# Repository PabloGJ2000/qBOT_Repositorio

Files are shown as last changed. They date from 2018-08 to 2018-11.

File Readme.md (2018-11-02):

# qBOT_Repositorio

## Información
* Autor: Pablo García Jaén (twitter: [@pablogarciajaen](https://twitter.com/PabloGarciaJaen)  )
* Web: http://qbotproject.com/
* Licencia: Creative Common CC BY-NC-SA 
* qBOT está basado en el mismo concepto de los Nanobots de la película Big Hero 6.

## Materiales
| Artículo | Cantidad* |
| --- | --- |
| Arduino Nano | 1 |
| GearMotor N20 | 3 |
| Acoplamiento para el eje N20 (3mm) | 3 |
| GearMotor N20 Eje m4 | 3 |
| Servo Analog SUMO1109 | 3 |
| Aspas Servo | 3 |
| Imán Neodimio N42 9x3mm | 6 |
| Pin Macho (4 pines juntos) | 3 |
| Pin Hembra (4 pines juntos) | 12 |
| Driver de motores SN754410 | 3 |
| Extensor de pines MCP23008 | 1 |
| Potenciometro 10k | 3 |
| Tornillería | - |
| 3D | - |

* *CANTIDAD PARA UN qBOT

## Hazlo tu mismo (DIY)

`Parte 1: Cara A` 

#### 	Diseño:

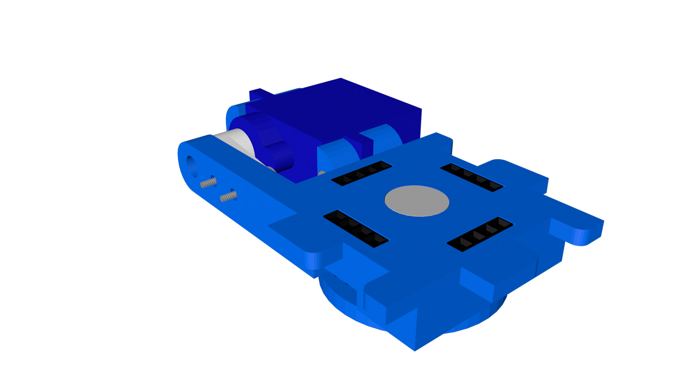
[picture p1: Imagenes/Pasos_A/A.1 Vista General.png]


#### 	Archivos 3D:

Haz click para descargarlas

- [CaraA.1_Pieza1.stl](https://github.com/PabloGarciaJaen/qBOT_Repositorio/blob/master/Archivos%203D/CaraA.1_Pieza1.stl)

- [CaraA.1_Pieza2.stl](https://github.com/PabloGarciaJaen/qBOT_Repositorio/blob/master/Archivos%203D/CaraA.1_Pieza2.stl)

- [CaraA.1_Pieza3.stl](https://github.com/PabloGarciaJaen/qBOT_Repositorio/blob/master/Archivos%203D/CaraA.1_Pieza3.stl)

//Nota_1: Los archivos están optimizados para una correcta impresión 3D sin soportes

//Nota_2: Es posible que algunas tengas que quitar el hueco para los tornillos o limar algunas partes.

#### 	Componentes:

| Componente | Cantdidad |
| --- | --- |
| Servo Analog SUMO1109 | 1 |
| Aspa servo | 1 |
| Imán Neodimio N42 9x3mm | 1 |
| Pin Hembra (4 pines juntos) | 3 |
| Tornillo eje servo | 1 |
| Tornillo anclaje | 2 |
| Tornillo soporte | 2 |

#### Montaje:

1. Pega las piezas *CaraA.1_Pieza1.stl* y *CaraA.1_Pieza2.stl*.

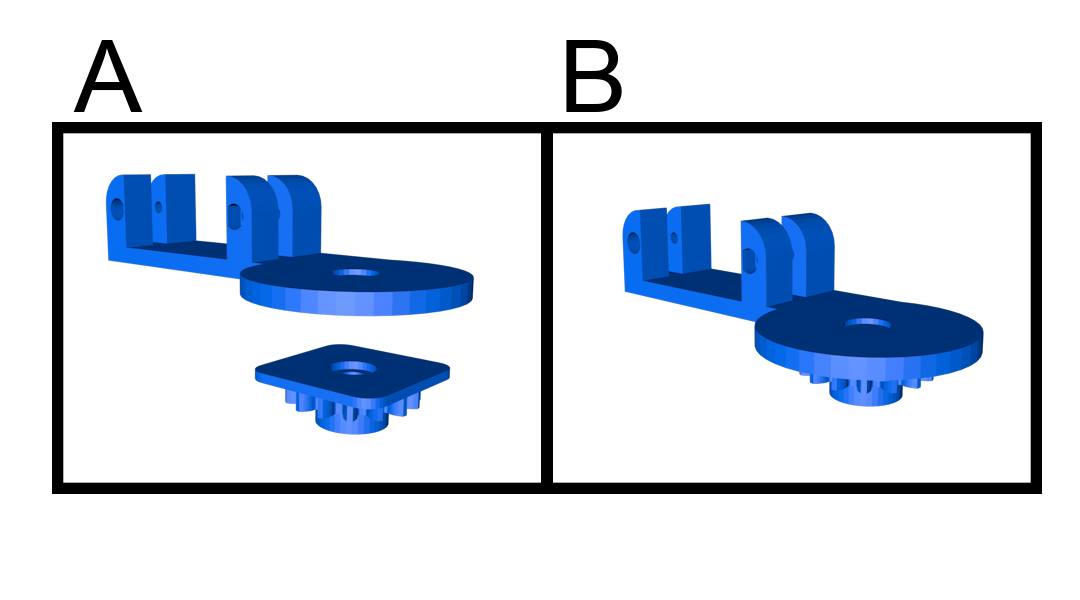
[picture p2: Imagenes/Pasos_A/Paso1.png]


2. Introduce el tornillo del eje por el aspa del servo.

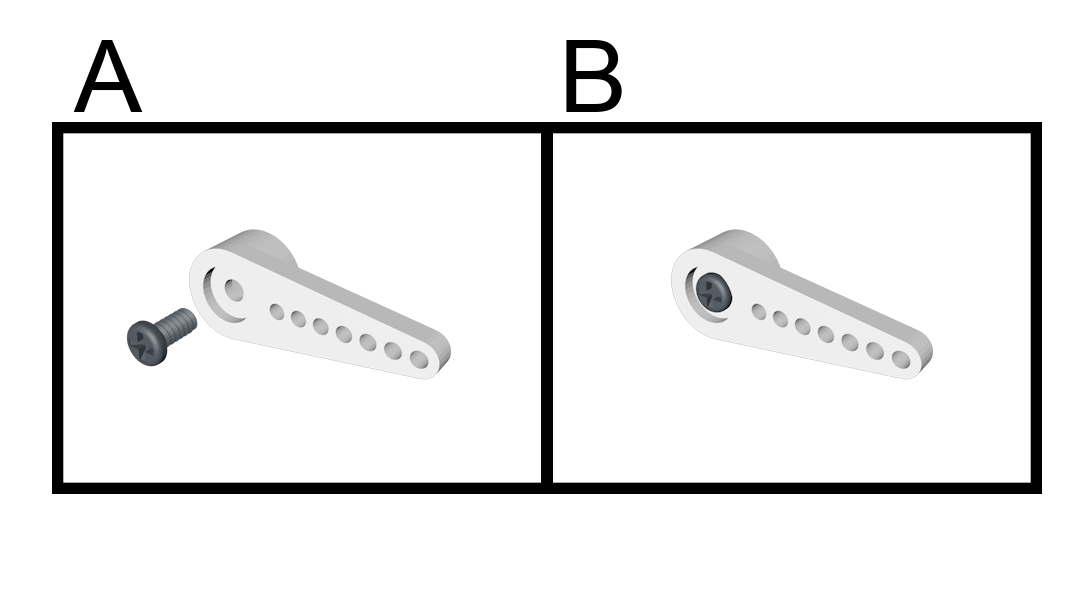
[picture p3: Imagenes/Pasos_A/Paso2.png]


3. Atornilla la pieza blanca del servo a *CaraA.1_Pieza3.stl*.

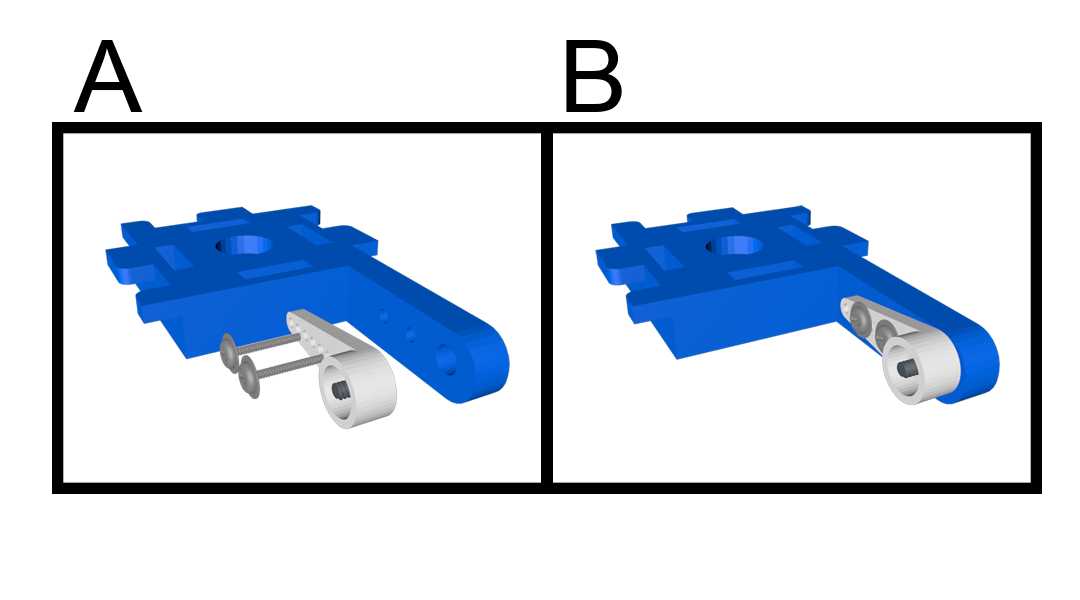
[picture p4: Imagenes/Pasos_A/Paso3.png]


4. Introduce el iman de neodimio y los pines hembra en sus correspondientes orificios.

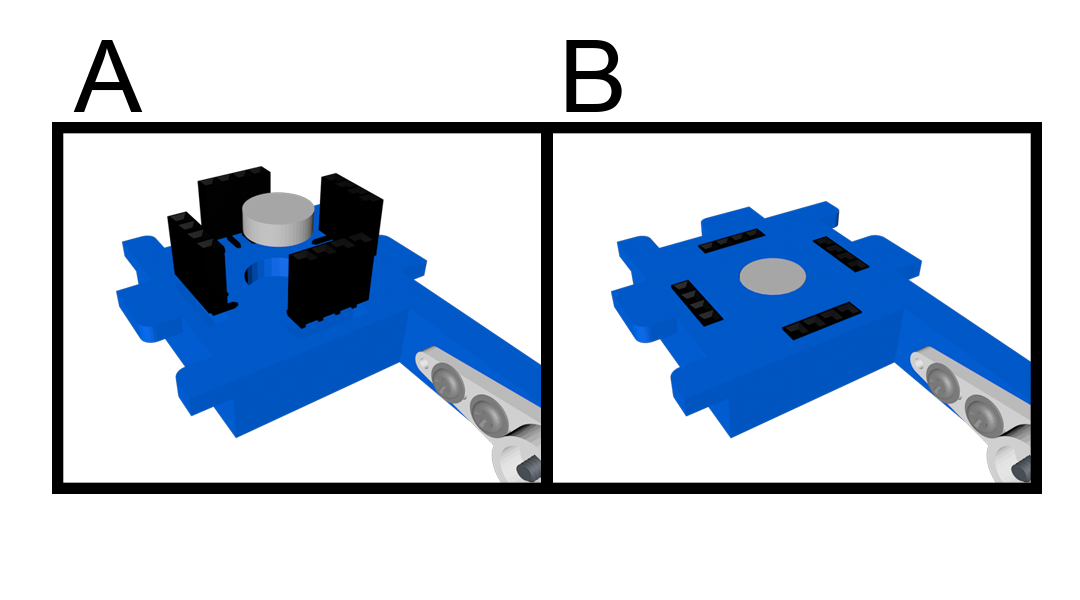
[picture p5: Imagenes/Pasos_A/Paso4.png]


5. Suelda los pines hembra siguiendo los **RECUADROS ROJOS** del siguiente esquemático.

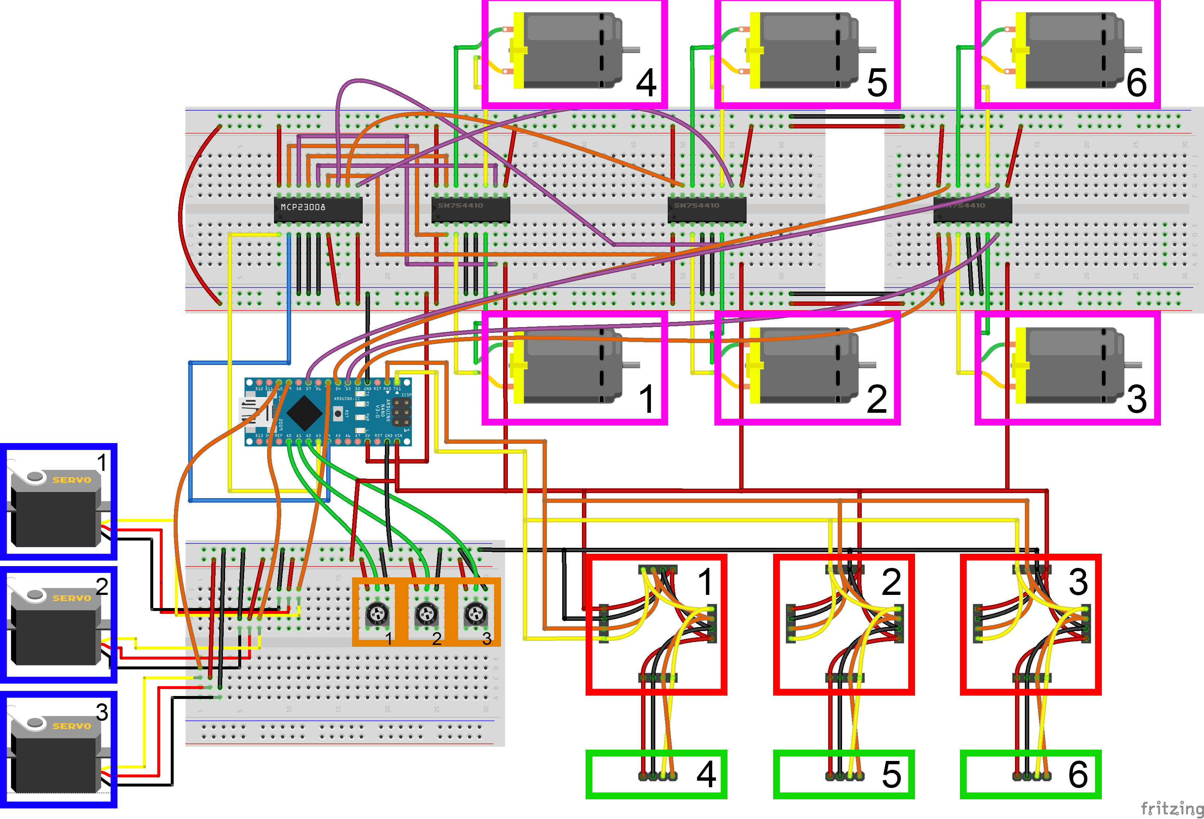
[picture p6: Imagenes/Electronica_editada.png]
!

6. Introduce el Servo en su hueco.

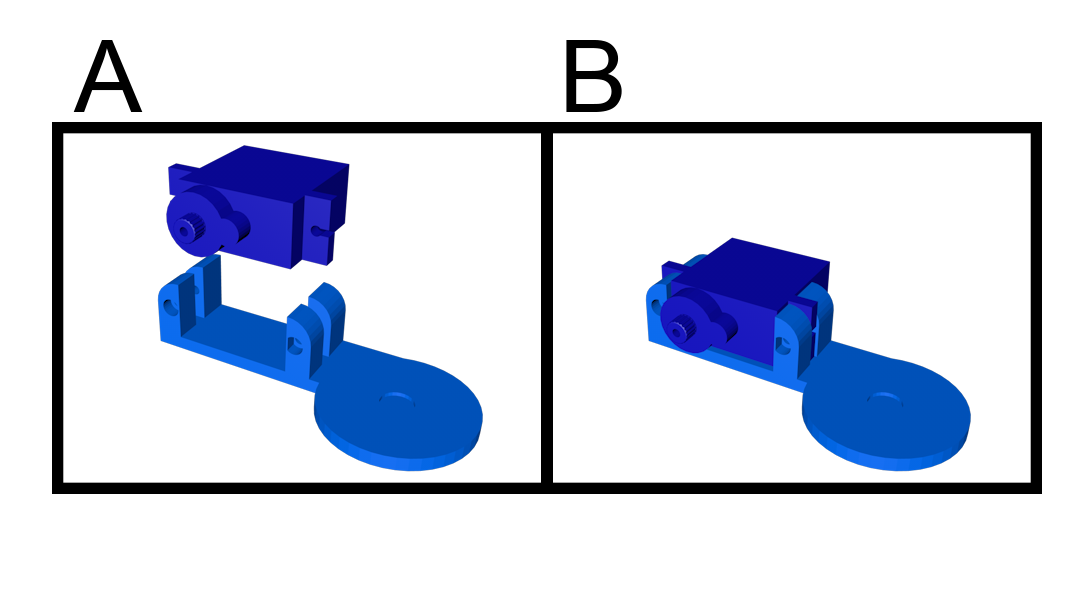
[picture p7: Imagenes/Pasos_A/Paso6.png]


7. Atornilla el Servo.

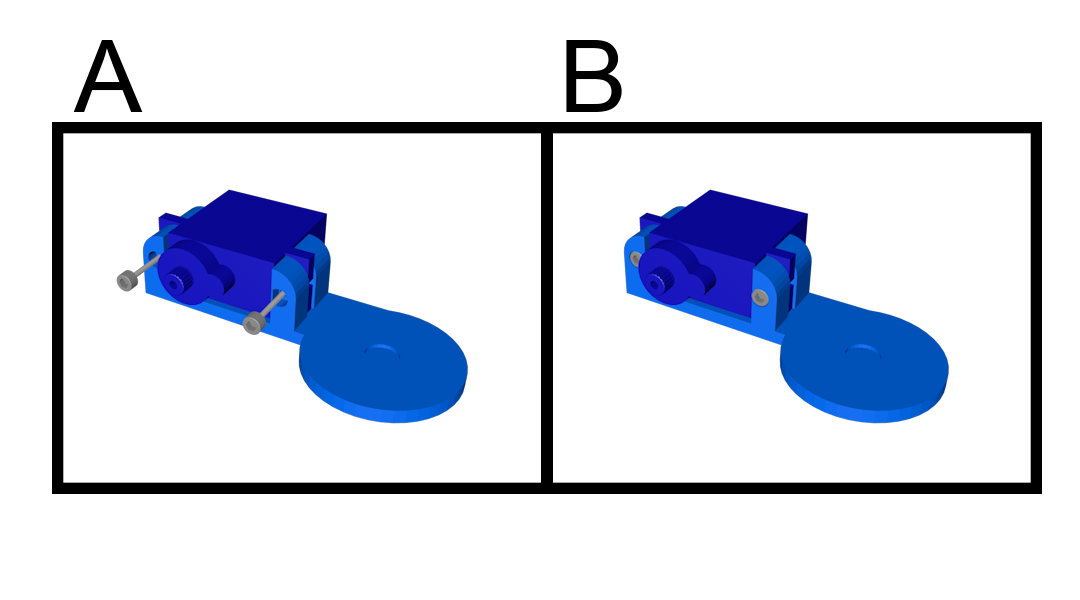
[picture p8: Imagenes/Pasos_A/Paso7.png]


8. Atornilla las dos partes con el tornillo del eje.

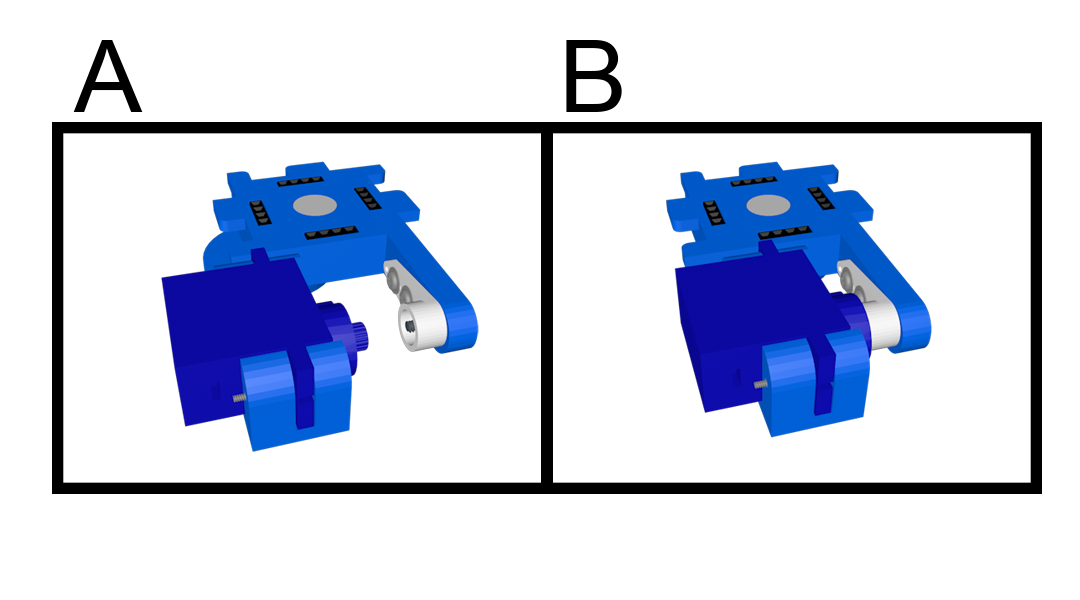
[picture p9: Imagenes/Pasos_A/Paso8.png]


9. Repite el mismo proceso hasta tener las caras A.1 A.2 y A.3. Los archivos 3D son los mismos para las 3 caras. 

`Parte 2: Cuerpo`

#### 	Diseño:

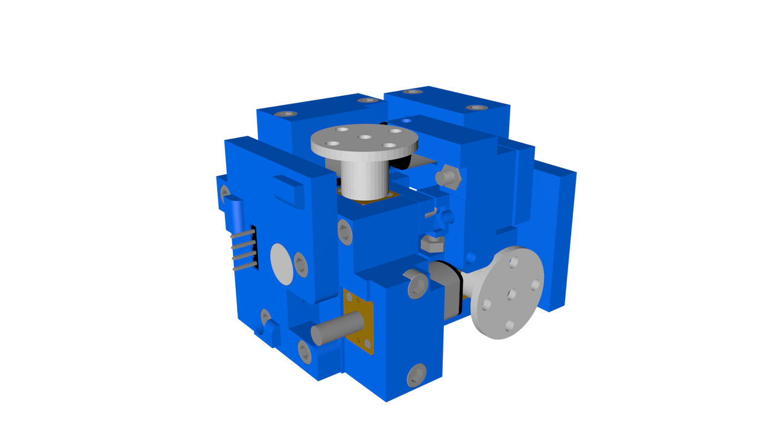
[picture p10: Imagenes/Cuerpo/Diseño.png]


#### 	Archivos 3D:

[Cuerpo_Pieza1.stl](https://github.com/PabloGarciaJaen/qBOT_Repositorio/blob/master/Archivos%203D/Cuerpo_Pieza1.stl)

[Cuerpo_Pieza2.stl](https://github.com/PabloGarciaJaen/qBOT_Repositorio/blob/master/Archivos%203D/Cuerpo_Pieza2.stl)

[Cuerpo_Pieza3.stl](https://github.com/PabloGarciaJaen/qBOT_Repositorio/blob/master/Archivos%203D/Cuerpo_Pieza3.stl)

[Cuerpo_Pieza4.stl](https://github.com/PabloGarciaJaen/qBOT_Repositorio/blob/master/Archivos%203D/Cuerpo_Pieza4.stl)

[Cuerpo_Pieza5.stl](https://github.com/PabloGarciaJaen/qBOT_Repositorio/blob/master/Archivos%203D/Cuerpo_Pieza6.stl)

[Cuerpo_Pieza6.stl](https://github.com/PabloGarciaJaen/qBOT_Repositorio/blob/master/Archivos%203D/Cuerpo_Pieza6.stl)

[Cuerpo_Pieza7.stl](https://github.com/PabloGarciaJaen/qBOT_Repositorio/blob/master/Archivos%203D/Cuerpo_Pieza7.stl)

[Cuerpo_Pieza8.stl](https://github.com/PabloGarciaJaen/qBOT_Repositorio/blob/master/Archivos%203D/Cuerpo_Pieza8.stl)

[Cuerpo_Pieza9.stl](https://github.com/PabloGarciaJaen/qBOT_Repositorio/blob/master/Archivos%203D/Cuerpo_Pieza9.stl)

[Cuerpo_Pieza10.stl](https://github.com/PabloGarciaJaen/qBOT_Repositorio/blob/master/Archivos%203D/Cuerpo_Pieza10.stl)

[Cuerpo_Pieza11.stl](https://github.com/PabloGarciaJaen/qBOT_Repositorio/blob/master/Archivos%203D/Cuerpo_Pieza11.stl)

[Cuerpo_Pieza12.stl](https://github.com/PabloGarciaJaen/qBOT_Repositorio/blob/master/Archivos%203D/Cuerpo_Pieza12.stl)

[Cuerpo_Pieza13.stl](https://github.com/PabloGarciaJaen/qBOT_Repositorio/blob/master/Archivos%203D/Cuerpo_Pieza13.stl)

//Nota_1: Los archivos están optimizados para una correcta impresión 3D sin soportes

//Nota_2: Es posible que algunas tengas que quitar el hueco para los tornillos o limar algunas partes.

#### 	Componentes:

| Componente | Cantdidad |
| --- | --- |
| GearMotor N20 eje M4 | 3 |
| GearMotor con eje sin rosca | 3 |
| Acoplamiento para N20 | 3 |
| Pin Macho (4 pines juntos) | 3 |
| Imán Neodimio N42 9x3mm | 3 |
| Tornillo Allen M3 10mm Cabeza Cilíndrica | 13 |
| Tornillo Allen M3 20mm Cabeza Cilíndrica | 10 |
| Tuerca M3 | 10 |

#### 	Montaje:

1. Corta la varilla de los motores de forma que dejes 10mm de rosca.

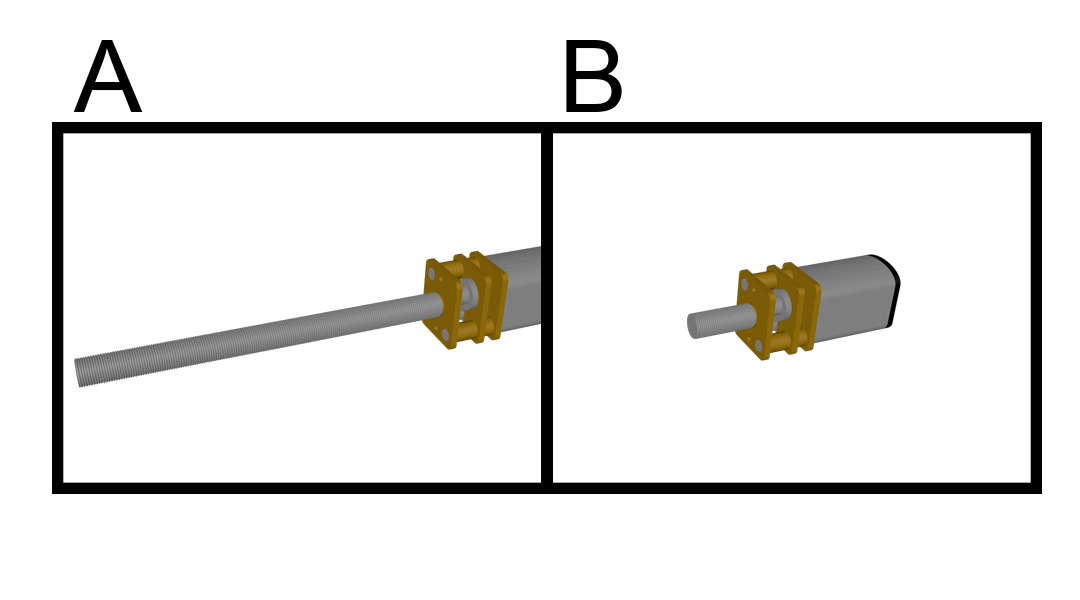
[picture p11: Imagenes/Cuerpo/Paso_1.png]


**//NOTA: Repite este paso 3 veces**

2. Une la el acoplamiento rígido a los motores no roscados.

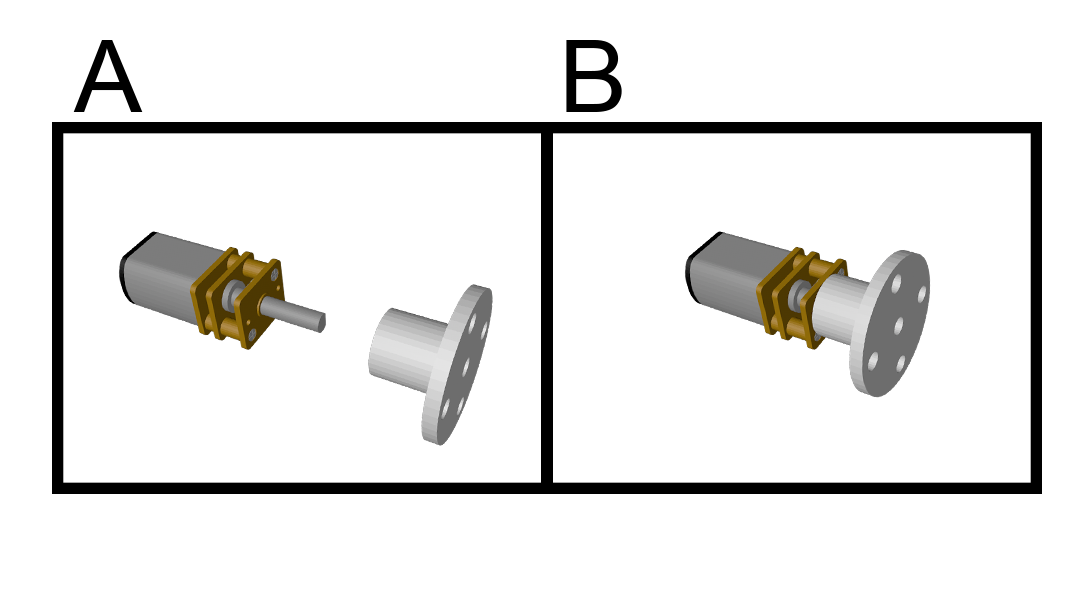
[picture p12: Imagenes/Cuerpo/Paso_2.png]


**//NOTA: Repite este paso 3 veces**

3. Atornilla *Cuerpo_Pieza1.stl* y *Cuerpo_Pieza2.stl* introduciendo el motor con eje.

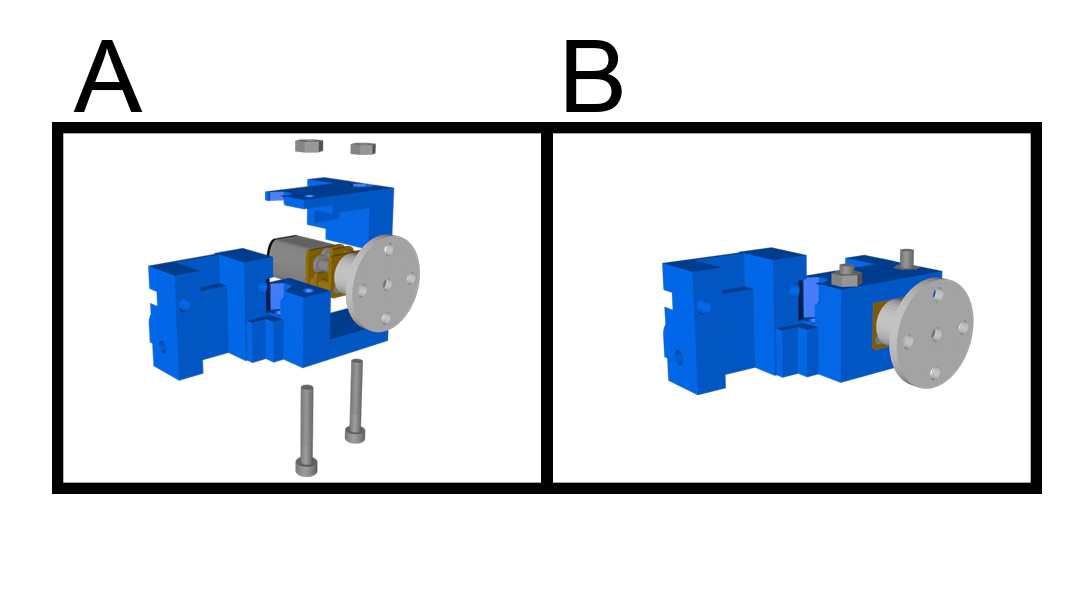
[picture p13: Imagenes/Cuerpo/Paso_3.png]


4. Atornilla *Cuerpo _Pieza3.stl* junto a la parte resultante del paso 3, introduciendo otro de los motores con eje.

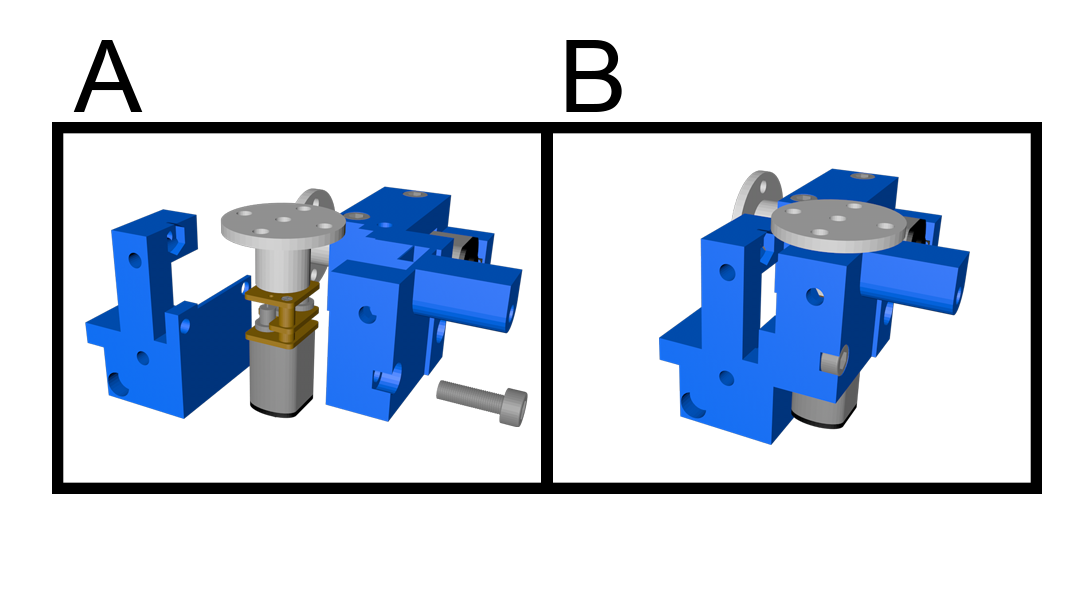
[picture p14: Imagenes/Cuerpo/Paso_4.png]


5. Introduce el último motor con eje en su correspondiente hueco y fijalo con *Cuerpo_Pieza4.stl*.

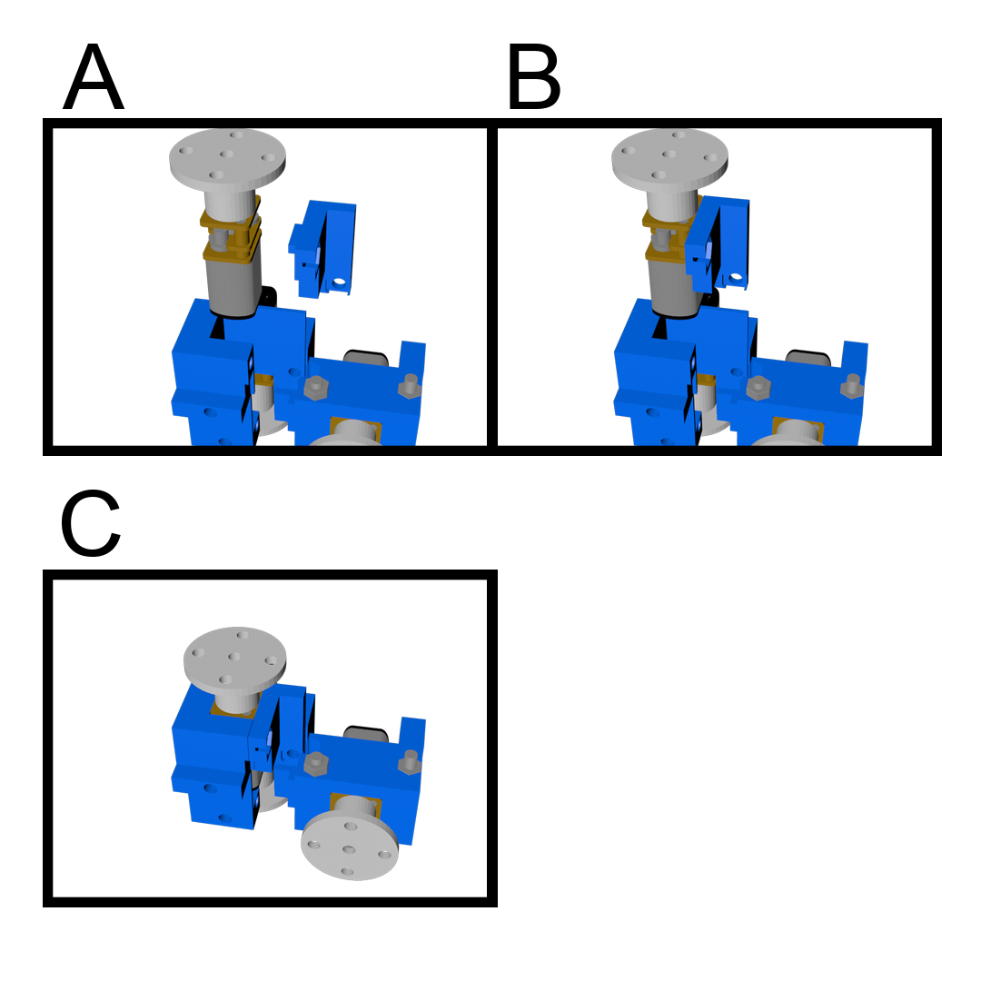
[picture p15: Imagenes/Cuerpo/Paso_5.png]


6. Atornilla el paso anterior.

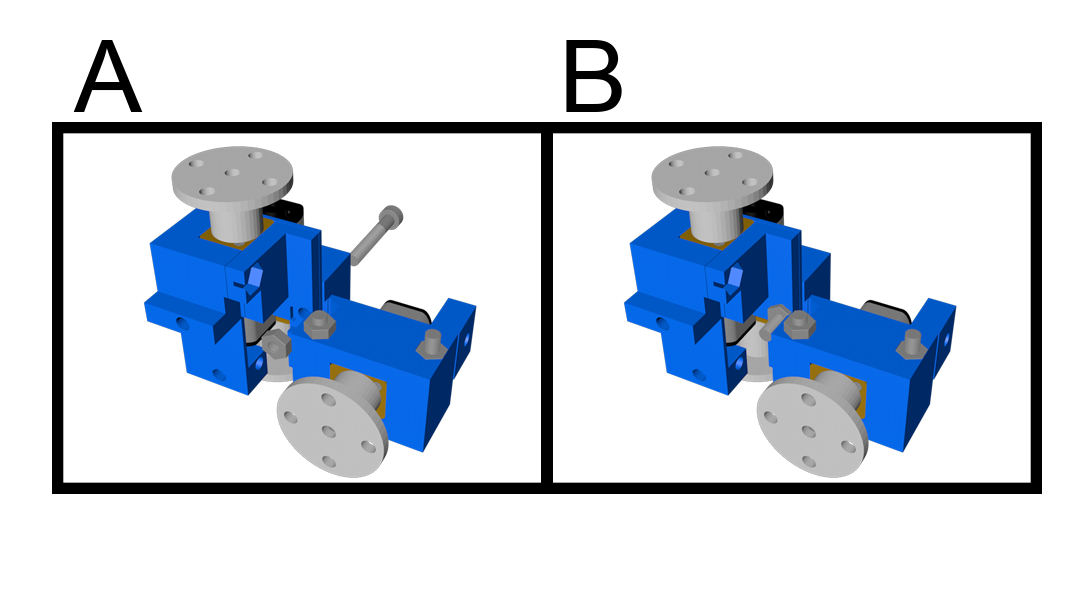
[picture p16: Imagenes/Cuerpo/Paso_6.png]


7. Introduce otro de los gearmotor y atornillalo junto a *Cuerpo_Pieza5*.

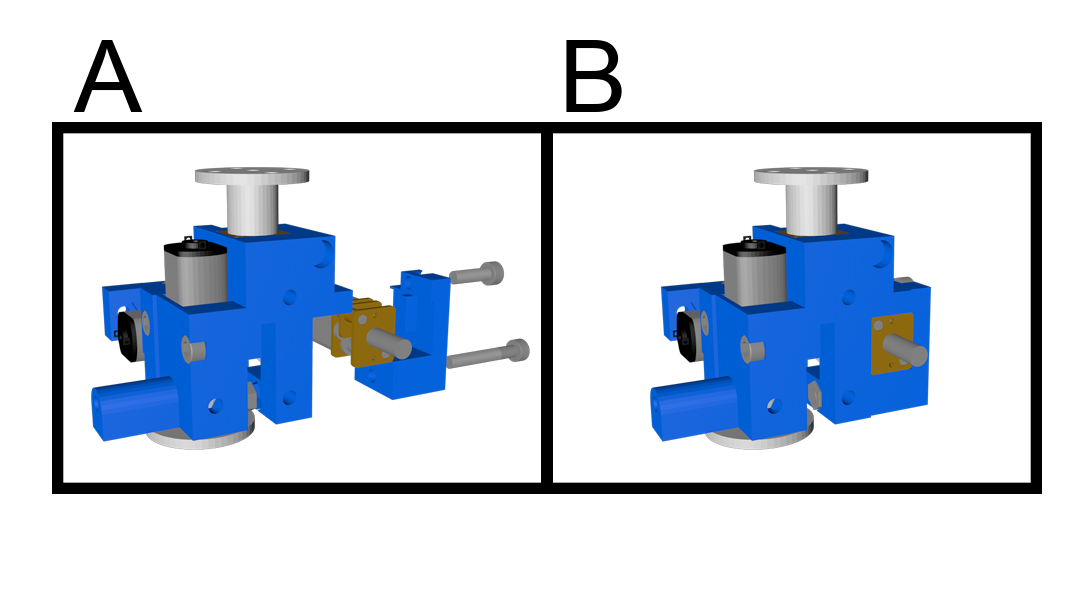
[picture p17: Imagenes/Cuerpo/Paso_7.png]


8. Atornilla *Cuerpo_Pieza6* junto al resto de la estructura.

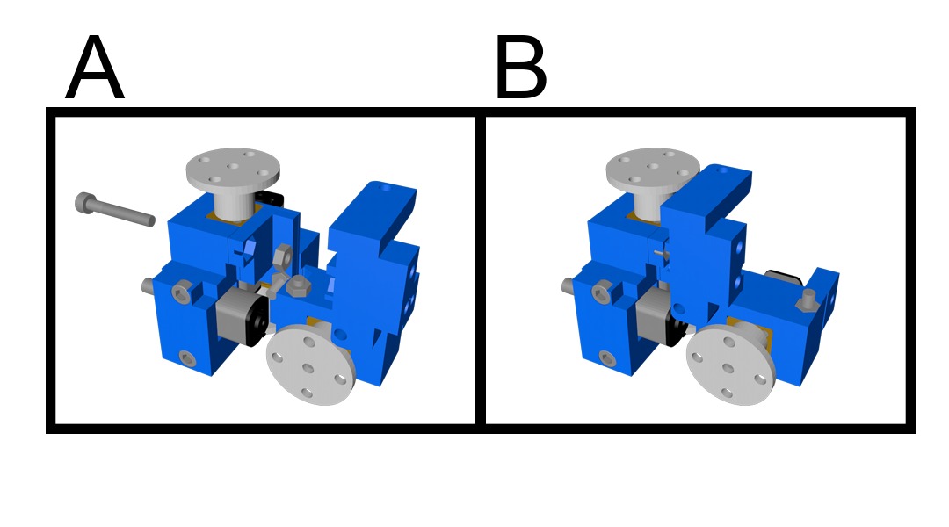
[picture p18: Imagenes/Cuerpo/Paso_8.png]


9. Atornilla *Cuerpo_Pieza7* junto al resto del cuerpo.

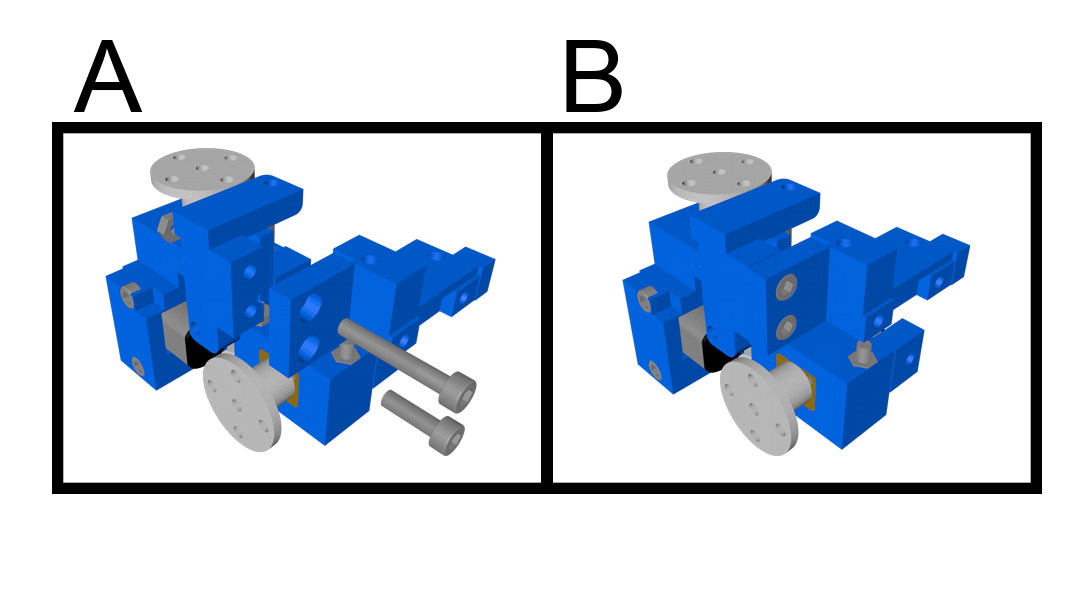
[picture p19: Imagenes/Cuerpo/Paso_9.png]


10. Atornilla uno de los gearmotor con rosca y *Cuerpo_Pieza8* a la estructura.

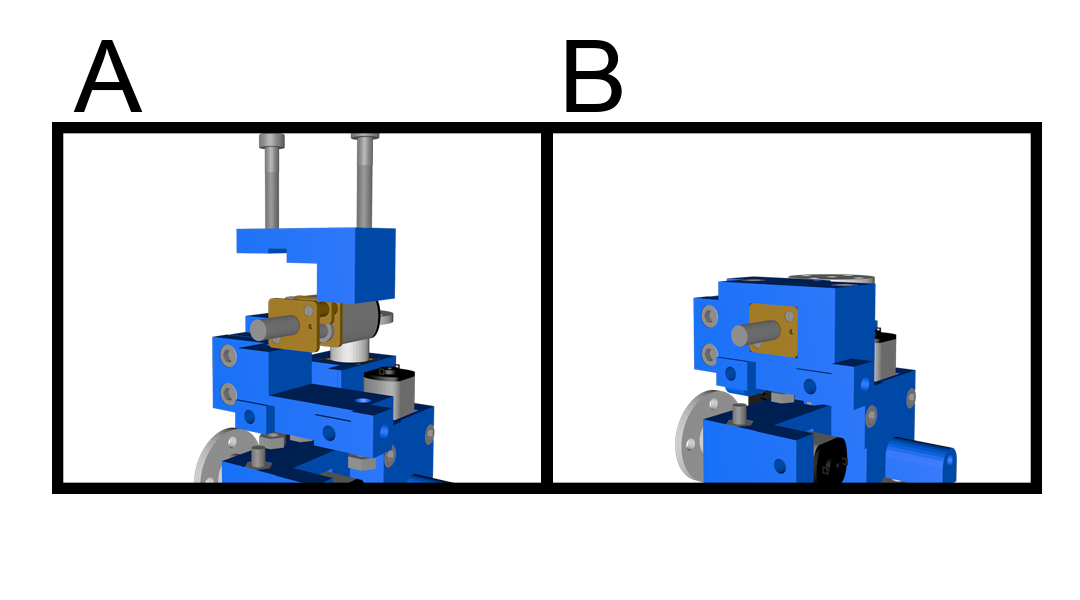
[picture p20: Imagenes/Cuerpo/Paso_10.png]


11. Pon los 4 pines macho, introduce el imán y atornilla *Cuerpo_Pieza9*. Recomendamos que introduzcas el iman y los pines (con cables soldados) antes de atornillarlo.

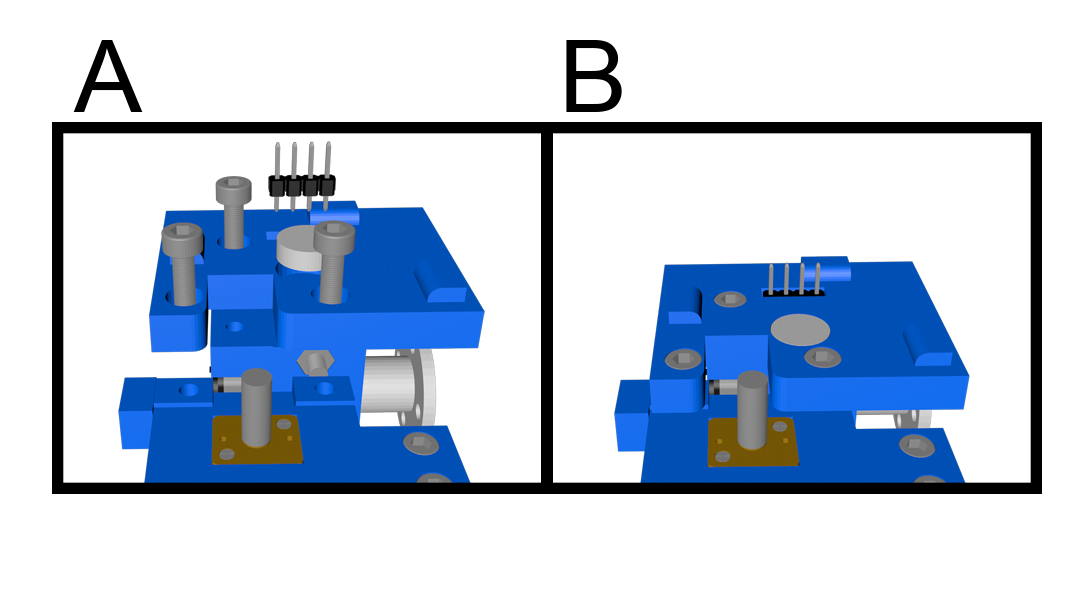
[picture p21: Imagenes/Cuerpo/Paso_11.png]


12. Pon los 4 pines macho, introduce el imán y atornilla *Cuerpo_Pieza10*. Recomendamos que introduzcas el iman y los pines(con cables soldados) antes de atornillarlo.

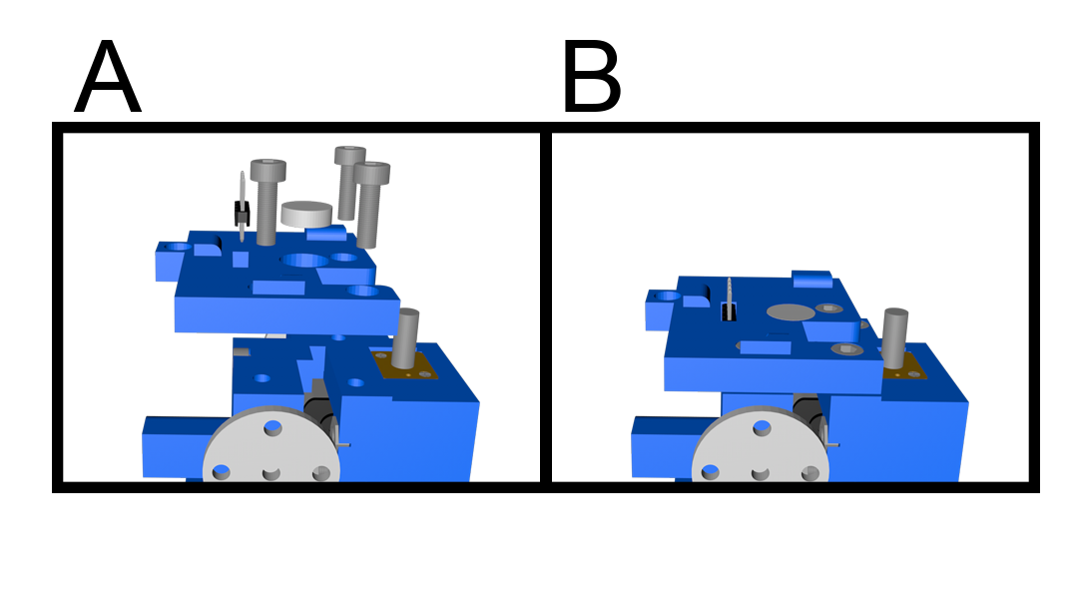
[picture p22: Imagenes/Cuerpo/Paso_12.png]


13. Atornilla el último gearmotor junto a *Cuerpo_Pieza11* y a *Cuerpo_Pieza12*

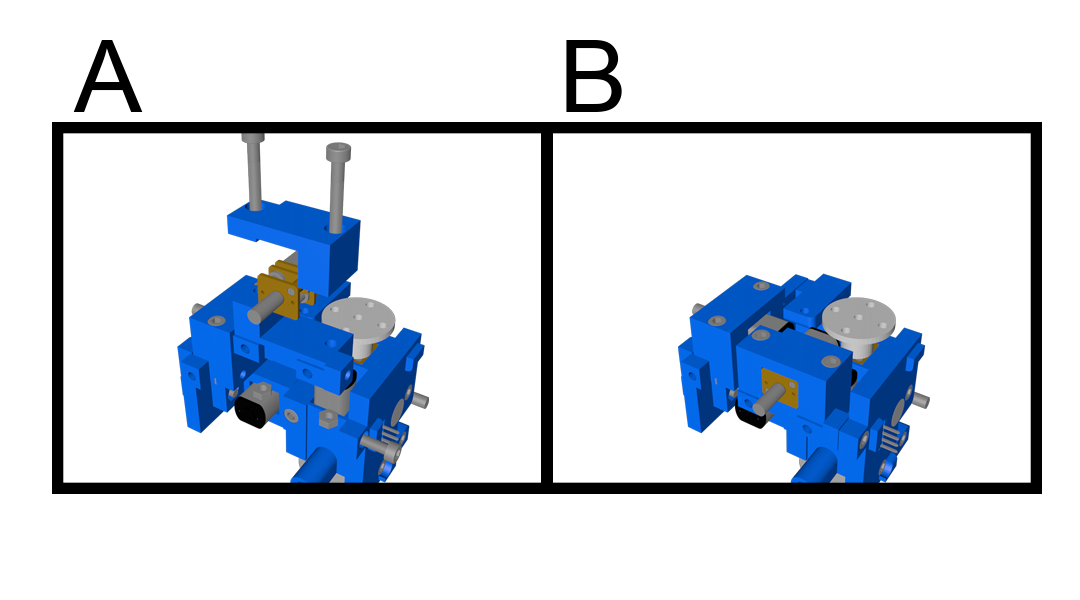
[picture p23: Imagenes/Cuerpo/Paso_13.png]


14. Pon los 4 pines macho, introduce el imán y atornilla *Cuerpo_Pieza13*. Recomendamos que introduzcas el iman y los pines(con cables soldados) antes de atornillarlo.

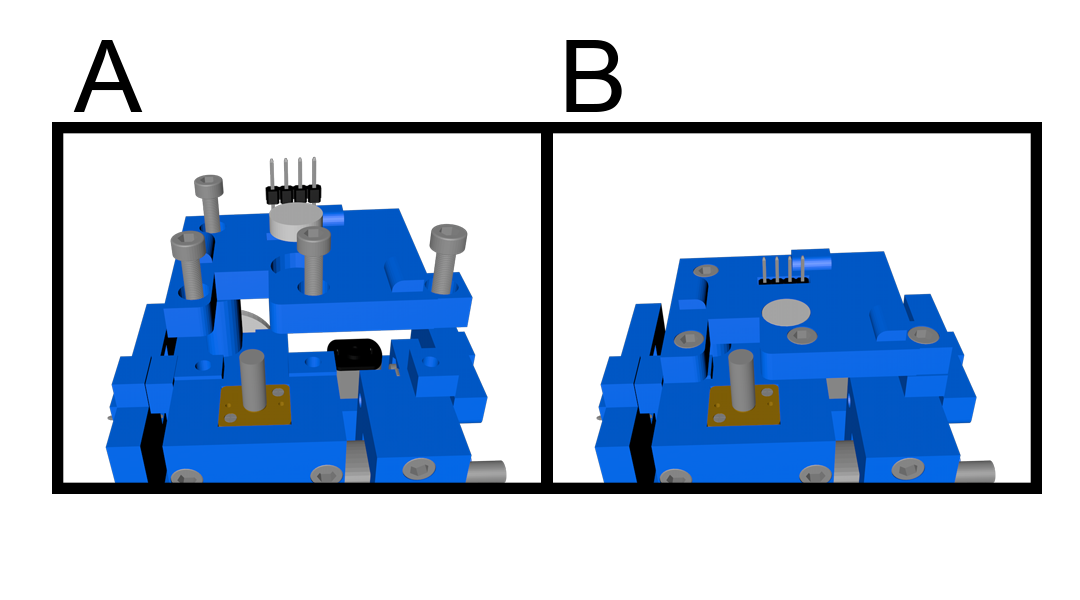
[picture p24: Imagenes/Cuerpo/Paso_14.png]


`Parte 3: Ejes`

1. Pegamos el soporte del potenciometro y el potenciometro. Después introducimos los 2 engranajes.

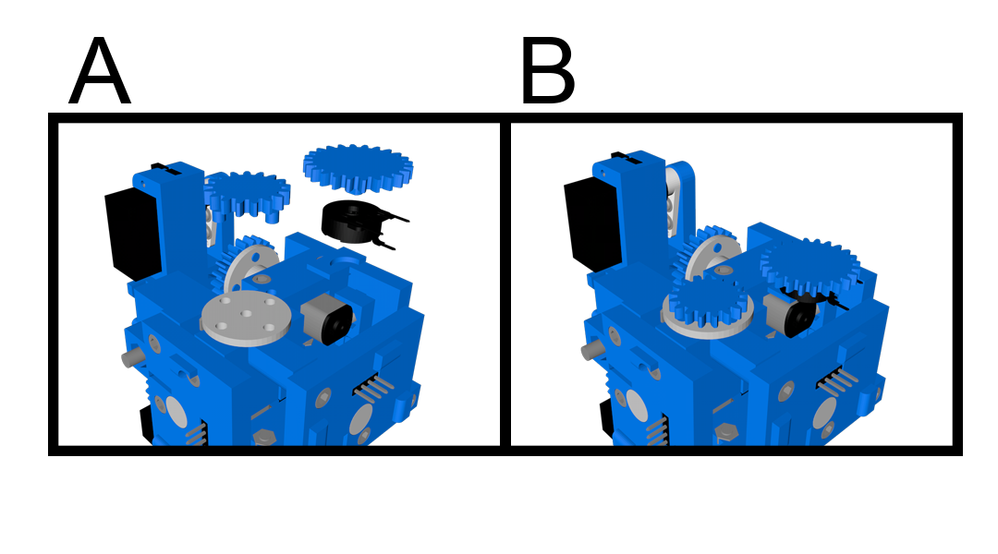
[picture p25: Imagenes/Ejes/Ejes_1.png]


2. Atornillamos los ejes al cuerpo.

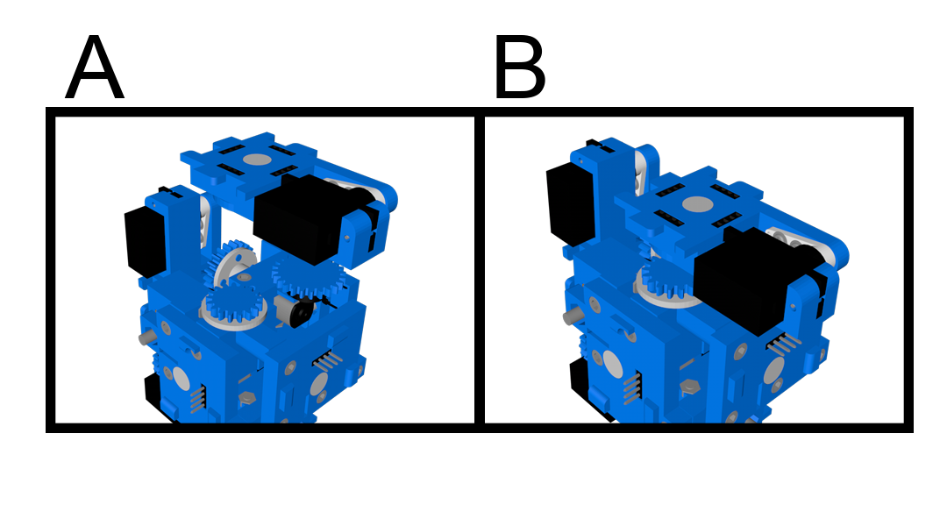
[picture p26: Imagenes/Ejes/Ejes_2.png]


3. Repetimos este paso con las 3 caras del cubo.

`Parte 4: Electrónica`
1. Suelda toda la electrónica siguiendo el siguiente esquemñatico
!

`Parte 5: Programación`
1. Compila y sube el siguiente código en tu Arduino (cada uno en su respectivo qBOT)
[Code_BLUE.ino](https://github.com/PabloGarciaJaen/qBOT_Repositorio/blob/master/Code_BLUE_/Code_BLUE_.ino)
[Code_ORANGE.ino](https://github.com/PabloGarciaJaen/qBOT_Repositorio/blob/master/Code_ORANGE/Code_ORANGE.ino)

`Parte 6: Comparte`
Personaliza tu qBOT y súbelo para que los demás usuarios lo repliquen y lo disfruten.

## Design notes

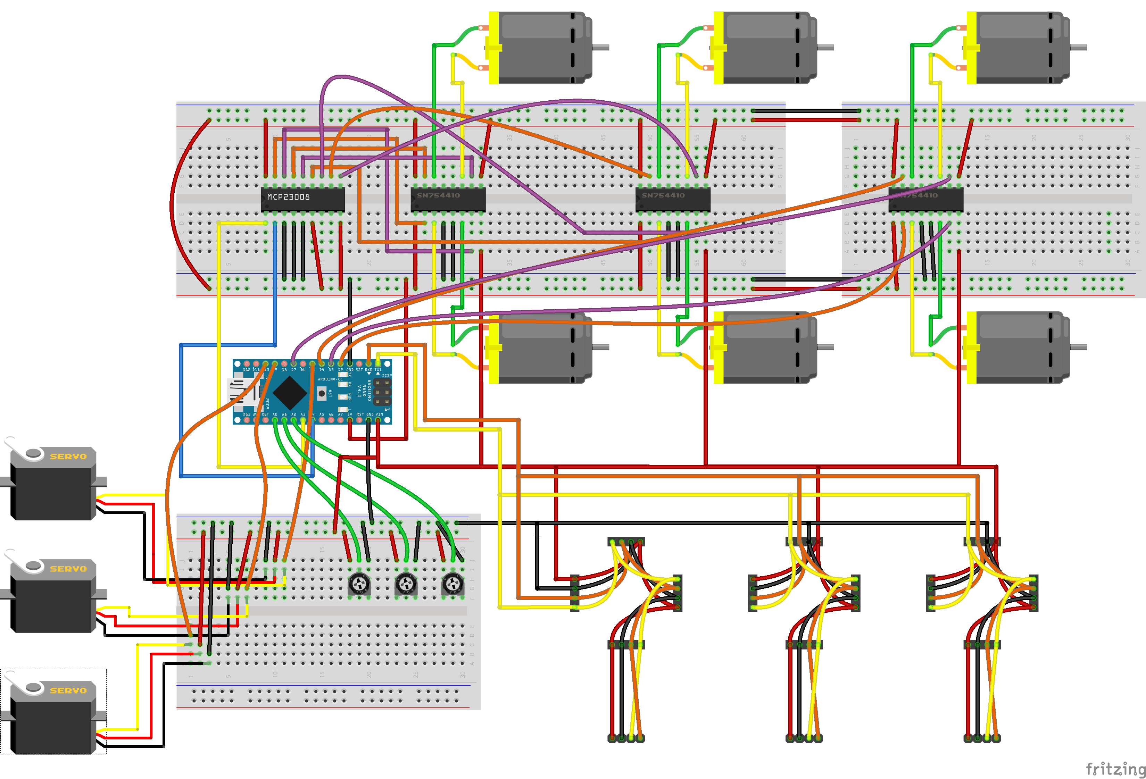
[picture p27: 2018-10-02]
Imagenes/Electronica.png

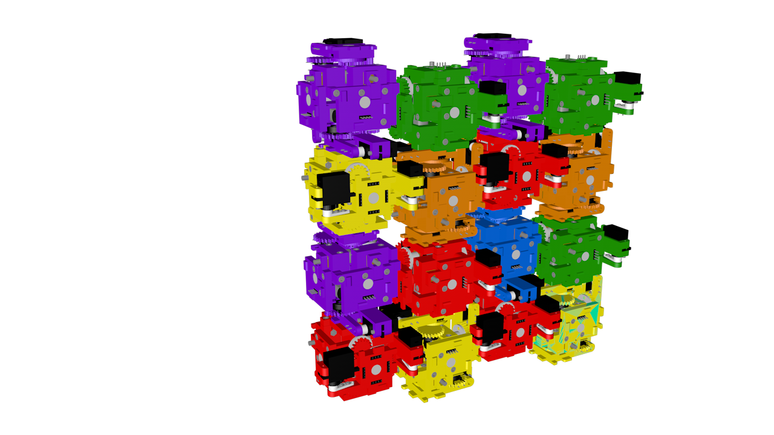
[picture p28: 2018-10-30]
Imagenes/qBOTs.png

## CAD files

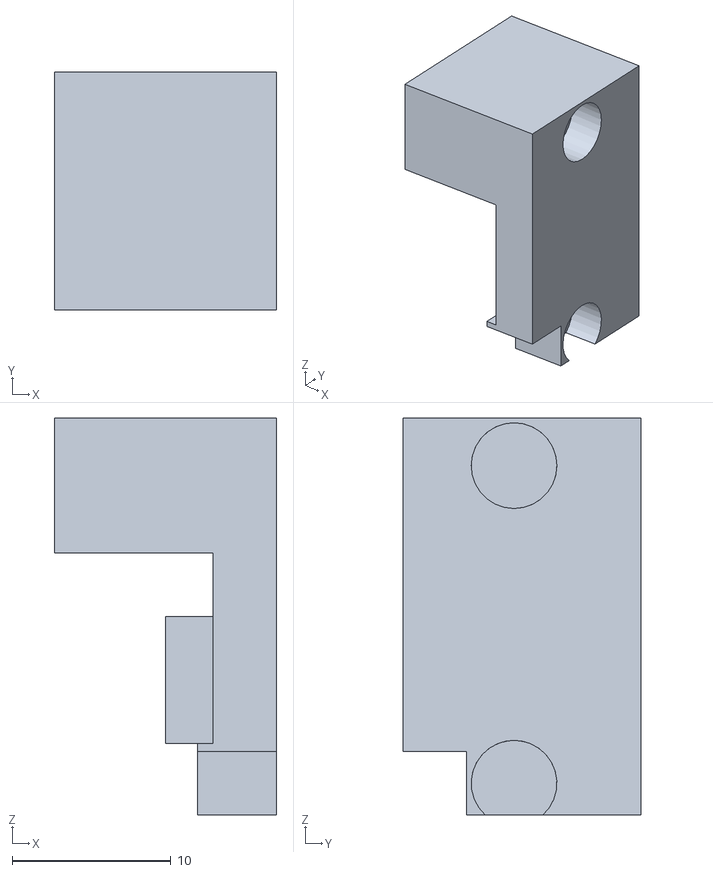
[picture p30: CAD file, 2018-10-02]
Archivos 3D/Cuerpo_Pieza5.stl
14.0 x 15.0 x 25.0

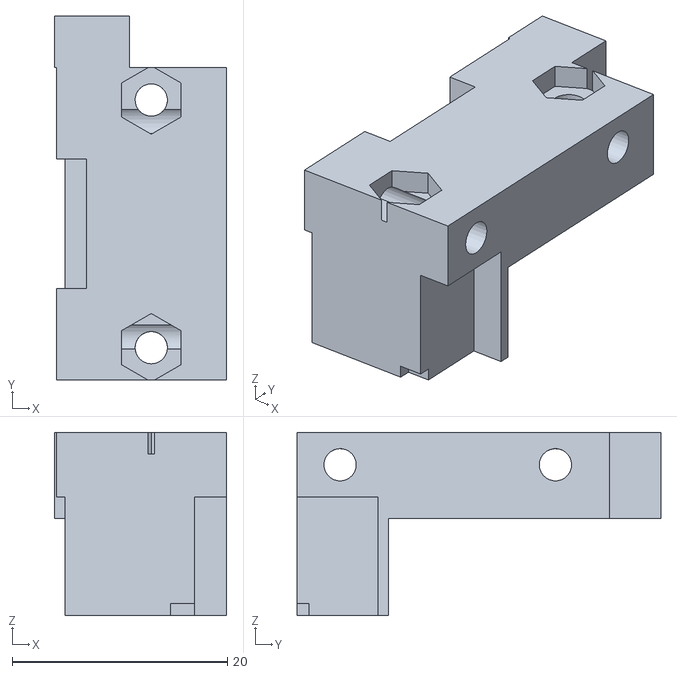
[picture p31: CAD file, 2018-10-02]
Archivos 3D/Cuerpo_Pieza12.stl
16.0 x 33.8 x 17.0

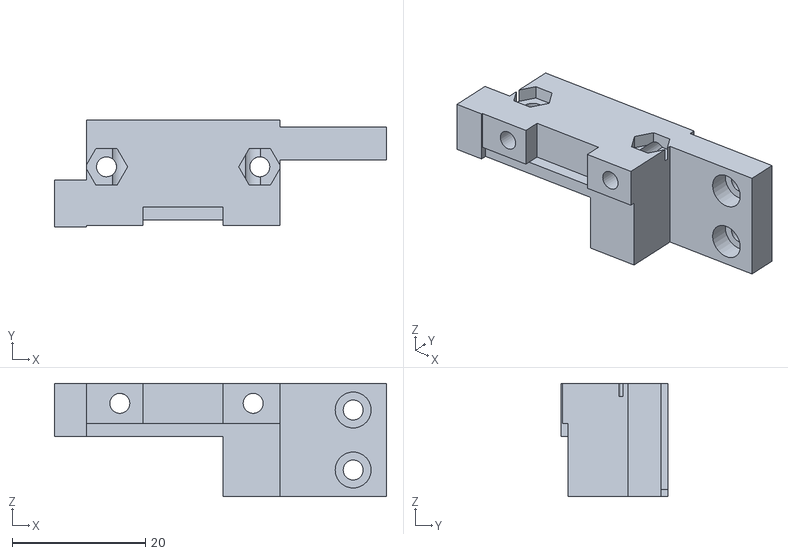
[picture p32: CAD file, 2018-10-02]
Archivos 3D/Cuerpo_Pieza7.stl
49.8 x 16.0 x 17.0

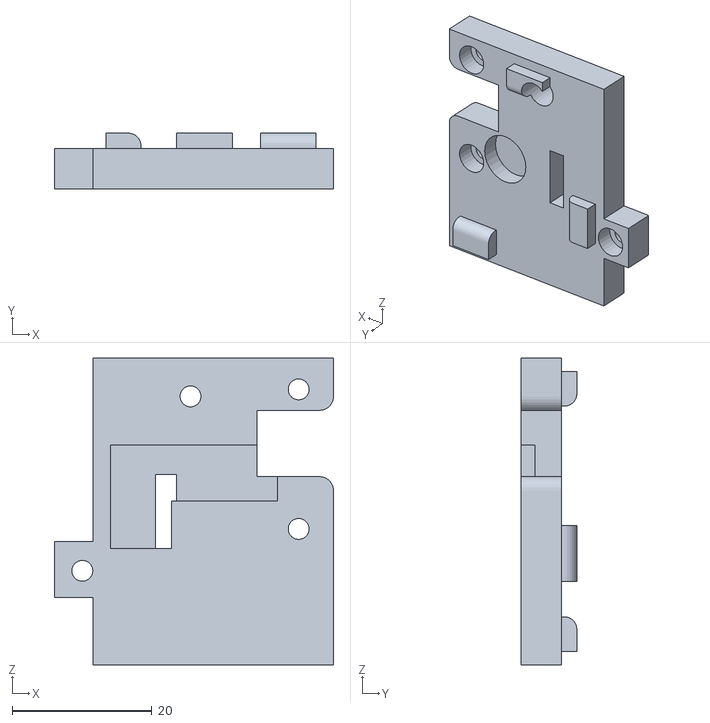
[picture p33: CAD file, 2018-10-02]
Archivos 3D/Cuerpo_Pieza10.stl
40.0 x 8.00 x 44.0

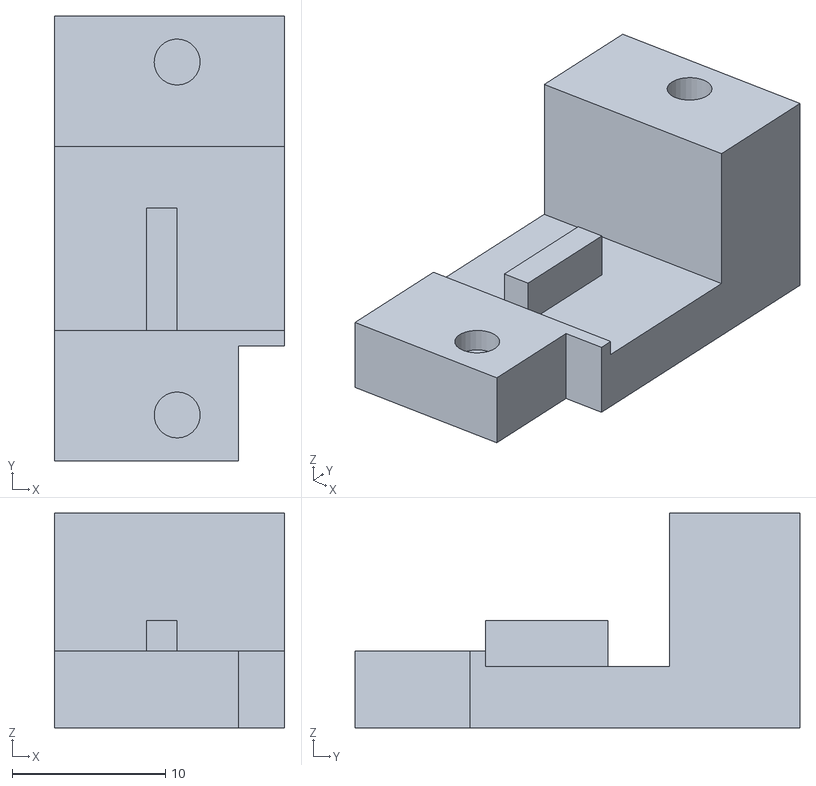
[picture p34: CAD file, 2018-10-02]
Archivos 3D/Cuerpo_Pieza11.stl
15.0 x 29.0 x 14.0

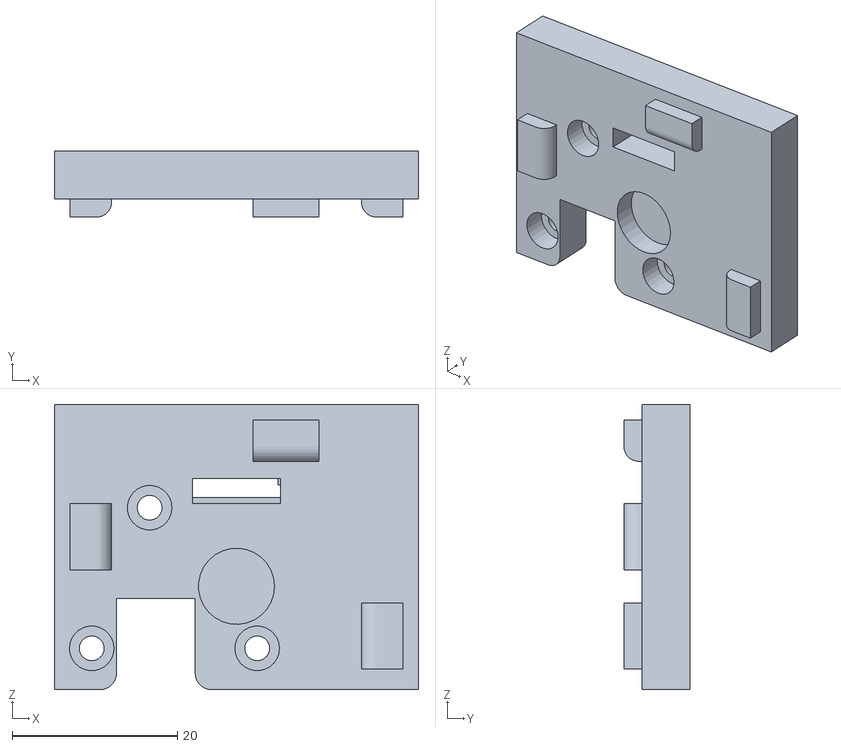
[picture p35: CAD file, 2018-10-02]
Archivos 3D/Cuerpo_Pieza9.stl
44.0 x 8.00 x 34.5

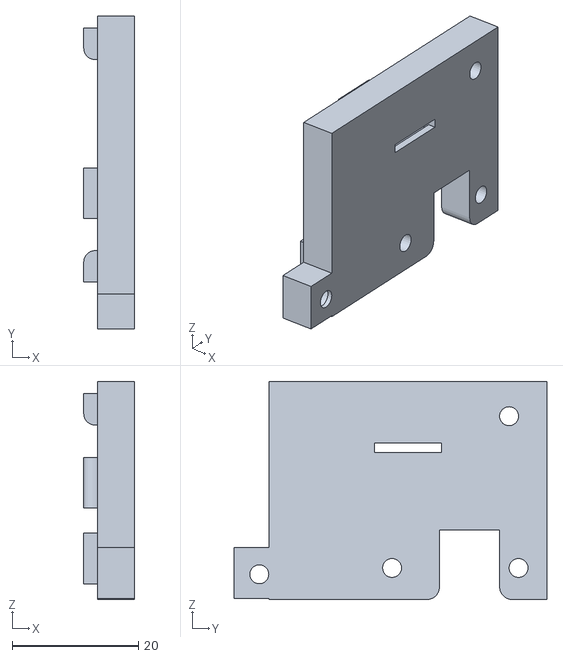
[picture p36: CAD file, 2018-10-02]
Archivos 3D/Cuerpo_Pieza13.stl
8.00 x 49.5 x 34.5

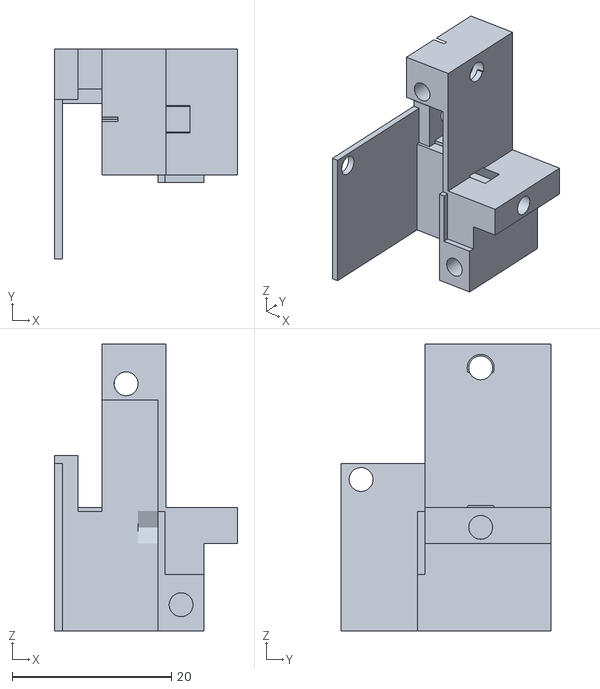
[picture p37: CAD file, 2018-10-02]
Archivos 3D/Cuerpo_Pieza3.stl
23.0 x 26.3 x 36.0

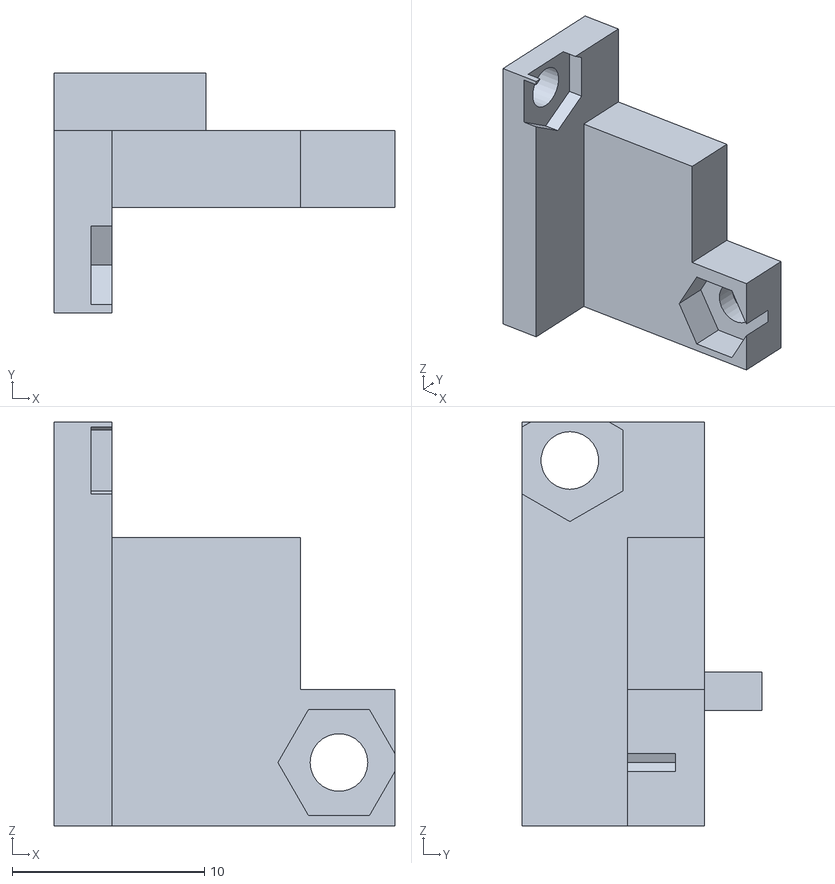
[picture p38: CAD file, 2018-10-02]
Archivos 3D/Cuerpo_Pieza4.stl
17.7 x 12.5 x 21.0

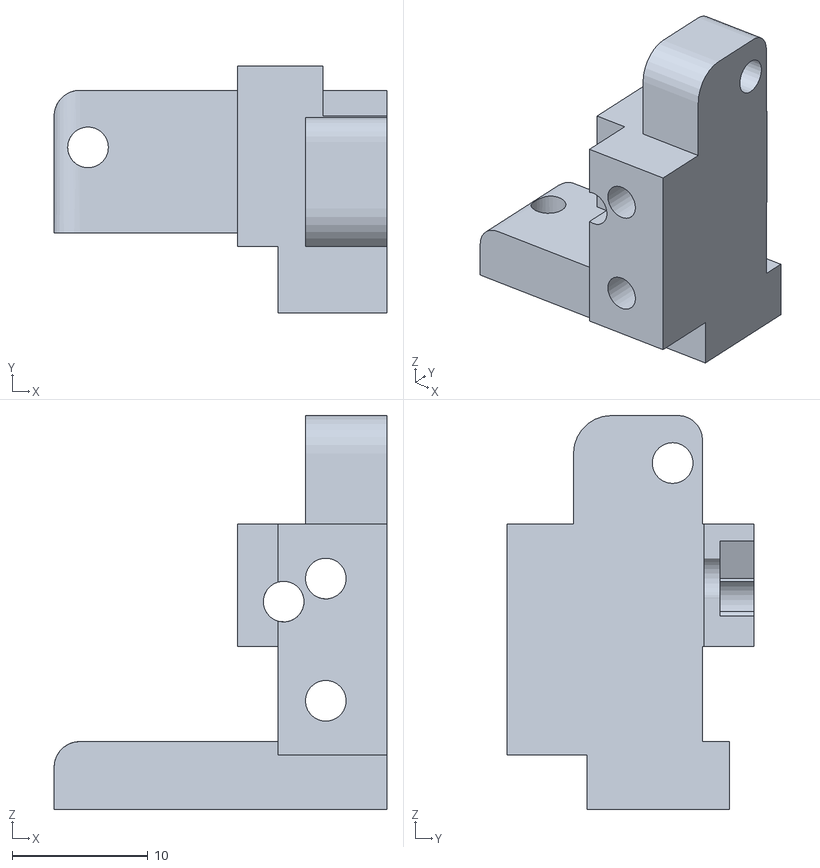
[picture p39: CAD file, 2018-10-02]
Archivos 3D/Cuerpo_Pieza6.stl
24.5 x 18.2 x 29.0

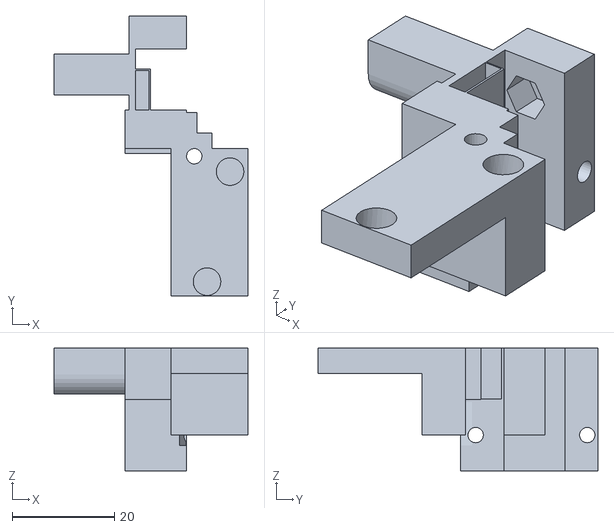
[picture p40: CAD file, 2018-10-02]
Archivos 3D/Cuerpo_Pieza1.stl
37.9 x 54.7 x 24.0

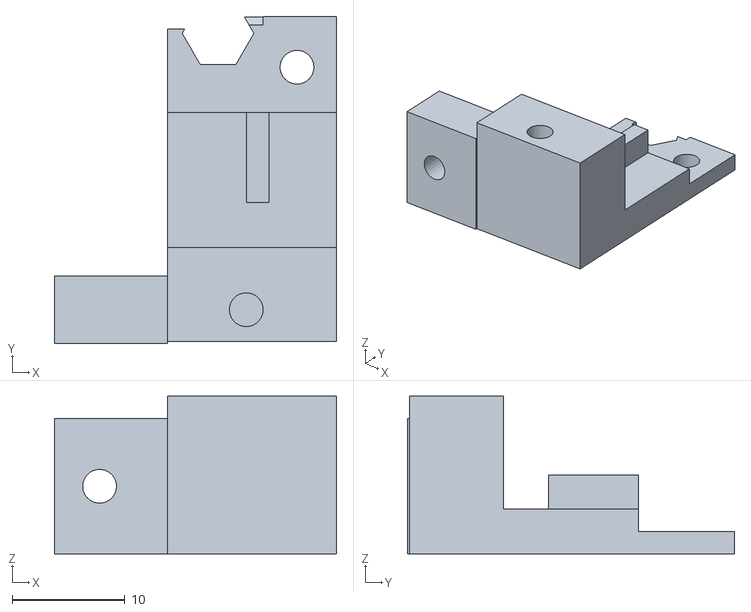
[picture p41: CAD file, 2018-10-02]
Archivos 3D/Cuerpo_Pieza2.stl
25.0 x 29.0 x 14.0

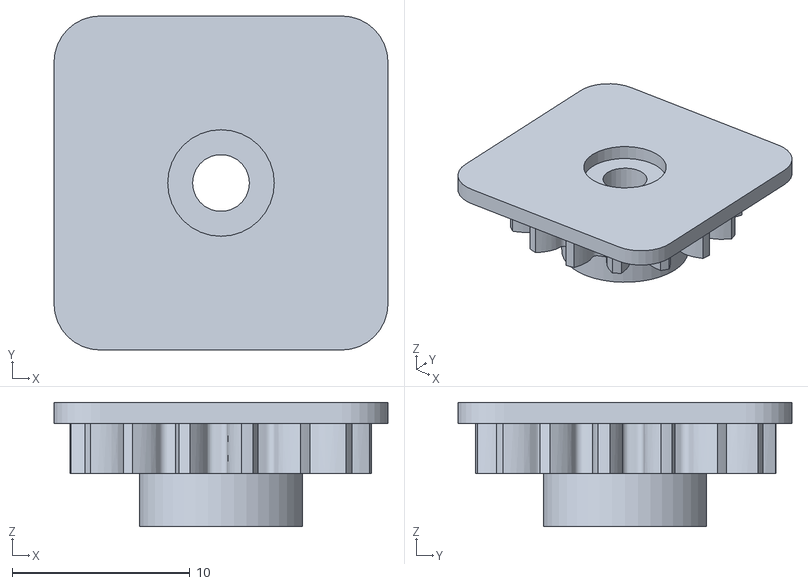
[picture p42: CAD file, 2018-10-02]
Archivos 3D/CaraA.1_Pieza2.stl
18.8 x 18.8 x 7.00

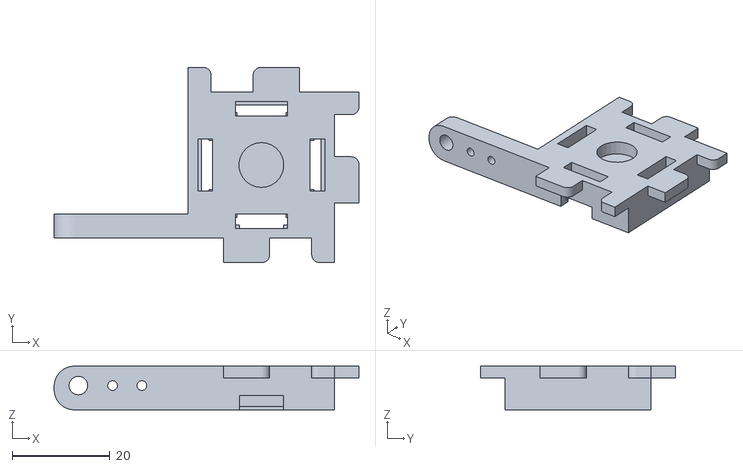
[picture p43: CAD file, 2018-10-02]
Archivos 3D/CaraA.1_Pieza3.stl
62.5 x 40.0 x 9.00

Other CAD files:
Archivos 3D/Cuerpo_Pieza8.stl
Archivos 3D/CaraA.1_Pieza1.stl

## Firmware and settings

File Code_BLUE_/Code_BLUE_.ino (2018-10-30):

/*Código [TEST] qBOT BLUE

   Autor: Pablo García Jaén
   Web: www.qbotproject.com
   Licencia: CC BY-NC-SA
   Repositorio: https://github.com/PabloGarciaJaen/qBOT_Repositorio

*/


//Librerias
#include <Wire.h>
#include "FabricaDigital_MCP23008.h"
#include <Servo.h>

const int MCP23008_I2C_DIR = 0x20; // Dirección I2C del MCP23008
FabricaDigital_MCP23008 pinesMotores(MCP23008_I2C_DIR);

//Declaramos los servos
Servo SERVO_A;
Servo SERVO_B;
Servo SERVO_C;

const int TIEMPO = 15;
const int TIEMPO_SERVOS = 10;

boolean activador_motor;
boolean activador_servo;
unsigned long tiempoAnterior = 0;

int GIRO = 0;

void TEMPORIZADOR() {
  //DEVOLVEMOS EL VALOR OPUESTO (1->0     0->1) DE activador_motor Y activador_servo.
  //ESTO NOS PERMITIRÁ QUE EL SERVO Y EL GEARMOTOR GIRE A UNA VELOCIDAD MAS LENTA.
  if (millis() - tiempoAnterior >= TIEMPO) { //si ha transcurrido el periodo programado
    activador_motor = !activador_motor;
    activador_servo = !activador_servo;
    tiempoAnterior = millis(); //guarda el tiempo actual como referencia
  }
}

void GIRAR_GEARMOTOR(int motor_X_A, int motor_X_B, int potenciometro, int valorMIN, int valorMAX ) {
  const int TIEMPO_GEARMOTOR = 20;
  int bucle = 1;
  while (bucle == 1) {
    int valorPOT;
    valorPOT = analogRead(potenciometro);
    Serial.println(valorPOT);

    //ESTA FUNCION NOS DEVOLVERÁ EL OPUESTO DE LA VARIABLE activador_motor CADA CIERTO TIEMPO.
    //GRACIAS A ESTO, LOS MOTORES SOLO SE ACTIVARÁN UNA VEZ DE CADA X MILISEGUNDO, REDUCIENDO SU VELOCIDAD.
    TEMPORIZADOR();

    if (activador_motor == 1) {  //ENTRAMOS SI NOS LO PERMITE LA FUNCION TEMPORIZADOR();
      if (valorPOT < valorMIN) {      //SI EL VALOR QUE LEEMOS DEL POTENCIOMETRO ES MENOR QUE EL MINIMO GIRAMOS HACIA UN LADO.
        digitalWrite(motor_X_A, LOW);
        digitalWrite(motor_X_B, HIGH);
      }
      if (valorPOT > valorMAX) { //SI EL VALOR QUE LEEMOS DEL POTENCIOMETRO ES MAYOR QUE EL MAXIMO GIRAMOS HACIA EL OTRO LADO.
        digitalWrite(motor_X_A, HIGH);
        digitalWrite(motor_X_B, LOW);
      }
      if ((valorPOT >= valorMIN) && (valorPOT <= valorMAX)) {  //SI EL VALOR QUE LEEMOS DEL POTENCIOMETRO ESTÁ COMPRENDIDO ENTRE EL MÍNIMO Y EL MÁXIMO PARAMOS LOS MOTORES.
        digitalWrite(motor_X_A, LOW);
        digitalWrite(motor_X_B, LOW);
        bucle = 0;
        return;
      }
    }

    if (activador_motor == 0) {   //SI LA FUNCION TEMPORIZADOR(); NOS DEVUELVE UN 0, APAGAMOS LOS MOTORES.
      digitalWrite(motor_X_A, LOW);
      digitalWrite(motor_X_B, LOW);
    }
  }
}

void DESPEGAR_GEARMOTOR(int motor_X_A, int motor_X_B) {
  pinesMotores.digitalWrite(motor_X_A, HIGH);
  pinesMotores.digitalWrite(motor_X_B, LOW);
  delay(4500);
  pinesMotores.digitalWrite(motor_X_A, LOW);
  pinesMotores.digitalWrite(motor_X_B, LOW);

}

void JUNTAR_GEARMOTOR(int motor_X_A, int motor_X_B) {
  pinesMotores.digitalWrite(motor_X_A, LOW);
  pinesMotores.digitalWrite(motor_X_B, HIGH);
  delay(4000);
  pinesMotores.digitalWrite(motor_X_A, LOW);
  pinesMotores.digitalWrite(motor_X_B, LOW);

}

void GIRAR_SERVO(int servo, int gradosA, int gradosB) {
  int pos;
  //SI GRADOA ES MENOR QUE GRADOB SIGNIFICA QUE TENEMOS QUE IR AUMENTANDO LOS GRADOS PROGRESIVAMENTE.
  if (gradosA < gradosB ) {
    for (pos = gradosA; pos <= gradosB; pos += 1) {
      switch (servo) {
        case 1:
          SERVO_A.write(pos);
          break;
        case 2:
          SERVO_B.write(pos);
          break;
        case 3:
          SERVO_C.write(pos);
          break;
      }
      delay(TIEMPO_SERVOS);
    }
  }
  //SI GRADOA ES MAYOR QUE GRADOB SIGNIFICA QUE TENEMOS QUE IR DISMINUYENDO LOS GRADOS PROGRESIVAMENTE.
  if (gradosA > gradosB) {
    for (pos = gradosA; pos >= gradosB; pos -= 1) {
      switch (servo) {
        case 1:
          SERVO_A.write(pos);
          break;
        case 2:
          SERVO_B.write(pos);
          break;
        case 3:
          SERVO_C.write(pos);
          break;
      }
      delay(TIEMPO_SERVOS);
    }
  }
}

void setup() {
  Serial.begin(9600);
  pinesMotores.begin();
  Serial.println("[BLUE] INICIADO");

  SERVO_A.attach(9);
  SERVO_B.attach(10);
  SERVO_C.attach(11);

  pinMode(2, OUTPUT);
  pinMode(3, OUTPUT);
  pinMode(4, OUTPUT);
  pinMode(7, OUTPUT);

  pinesMotores.pinMode(0, OUTPUT);
  pinesMotores.pinMode(1, OUTPUT);
  pinesMotores.pinMode(2, OUTPUT);
  pinesMotores.pinMode(3, OUTPUT);
  pinesMotores.pinMode(4, OUTPUT);
  pinesMotores.pinMode(5, OUTPUT);
  pinesMotores.pinMode(6, OUTPUT);
  pinesMotores.pinMode(7, OUTPUT);
}

bool activador = 1;
void loop() {
  /*NOMENCLATURA:
     GIRAR_SERVO(SERVO, GRADOS INICIO, GRADOS FINAL);
     GIRAR_GEARMOTOR(PIN A DEL MOTOR, PIN B DEL MOTOR, PIN DEL POTENCIOMETRO CORRESPONDIENTE, VALOR MINIMO DEL POT, VALOR MAXIMO DEL POT);
     DESPEGAR_GEARMOTOR(PIN A DEL GEARMOTOR, PIN B DEL GEARMOTOR);
     JUNTAR_GEARMOTOR(PIN A DEL GEARMOTOR, PIN B DEL GEARMOTOR);
  */

  if (activador == 1) {
    //POSICION INICIAL
    GIRAR_SERVO(1, 180, 0);
    GIRAR_GEARMOTOR(4, 7, A2, 490, 491);
    delay(10000);
    //DESPLEGAMOS EL SERVO PARA QUE EL QBOT NARANJA GIRE.
    GIRAR_GEARMOTOR(4, 7, A2, 490, 491);
    GIRAR_SERVO(1, 0, 180);
    delay(10000);
    GIRAR_SERVO(1, 150, 0);
    delay(12000);
    //DESPEGAR LADO
    DESPEGAR_GEARMOTOR(6, 7);
    delay(7000);
    //JUNTAR LADO
    JUNTAR_GEARMOTOR(6, 7);
    GIRAR_GEARMOTOR(4, 7, A2, 714, 715);
    delay(2000);
    GIRAR_GEARMOTOR(4, 7, A2, 714, 715);
    GIRAR_SERVO(1, 0, 180);
    delay(2000);
    GIRAR_SERVO(1, 150, 180);
    DESPEGAR_GEARMOTOR(2, 3);
    delay(500);
    GIRAR_SERVO(1, 180, 0);
    JUNTAR_GEARMOTOR(2, 3);
  }

  //CON ESTE CÓDIGO PODREMOS CONTROLAR EL QBOT DE FORMA MANUAL (CON EL TECLADO)
  if (Serial.available() > 0) {
    char caracter;
    caracter = Serial.read();
    Serial.println(caracter);
    if (caracter == 'A') {
      GIRAR_SERVO(1, 180, 0);
    }
    if (caracter == 'B') {
      GIRAR_GEARMOTOR(4, 7, A2, 490, 491);
    }
    if (caracter == 'C') {    //DESPLEGAR SERVO
      GIRAR_SERVO(1, 0, 180);
    }

    if (caracter == 'D') {    //[BLUE] DESPEGAR LADO
      DESPEGAR_GEARMOTOR(6, 7);
    }
    if (caracter == 'E') {    //[BLUE] JUNTAR LADO
      JUNTAR_GEARMOTOR(6, 7);
    }
    if (caracter == 'F') {
      GIRAR_GEARMOTOR(4, 7, A2, 709, 710);
    }
    if (caracter == 'G') {    //[BLUE] DESPEGAR ARRIBA
      DESPEGAR_GEARMOTOR(2, 3);
    }
    if (caracter == 'H') {    //[BLUE] JUNTAR ARRIBA
      JUNTAR_GEARMOTOR(2, 3);
    }
  }
}
